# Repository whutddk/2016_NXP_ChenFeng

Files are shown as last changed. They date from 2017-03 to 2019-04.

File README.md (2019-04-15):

# 2016年恩智浦杯全国大学生智能汽车大赛 

-------------------------------

* 有了前一年参赛的经验，更有了资金和赛道，一切就变得特别顺利
* 加入汽车学院参加比赛
* 参与其中的电轨竞速组和电轨节能组，拿下两个全国一等奖
    - 电轨竞速组负责：电路；代码工程搭建、验证、规范化；控制算法搭建、验证；传感器解决方案
    - 电轨节能组负责：电路；取电方案

----------------------------

### 背景
* 2016是比赛的改革年，出现了很多新组别（电轨，信标，双车超车）
* 我们参与的电轨组组别太新，规则摇摆不定
    - 是否取电
    - 传感器方案
* 赛初即做了取电解决方案，后来该方案移动至创意组。鉴于我校从来没有队伍参与创意（不知道保研政策），我们决定第一年试水创意，将创意作为备份组。

### 过程
* 这个组难点在传感器方案，官方给出的传统三点震荡方案很早进行了验证，距离太短。参考TI，LDC系列传感器，把所有手册看了一遍，发现LDC1614和LDC1314的方案最合适，评估版价格相同，选择精度更高的LDC1614。
* 区别于电磁，金属传感器只能看见线圈下面的赛道情况，没有电磁波传播的扩展，所以视角相对较小。前瞻越长，视角越小，控制越容易发散。
* 双线圈方案与三线圈方案
    - 传感器非线性问题非常严重，这一年探讨了非常多拟合线性化方案
    - 因为双线圈拟合有对称问题，改用三线圈拟合
* 控制
    - 舵机方向控制
        + 简单三参数PD
        + 因为队友机械能力很强，机械上大量非线性问题都解决了，简单的PID方向控制即可取得非常好的效果
    - 电机调速
        + 增量式PI
* 算法
    - 探讨过模糊控制并进行验证，因为风险较大，后面放弃使用
    - 后面采用简单PID加BNAG-BANG法进行控制
* 总结：如果要我总结智能车赛的三个要点
    - 全程参数线性化
        + 无论是修理机械，调整传感器，PID分段等，传感器多项式拟合，讨论的是线性控制，将非线性环节用各种手段处理掉，调参就很简单了
    - 保证控制实时性
        + 使用Cortex-M4处理器，运算主要集中在解算拟合函数，未使用到DSP，只要不使用模糊控制，我们组的控制实时裕量还是很足的（当然我自己也是验证过的）
        + 整个组的控制周期瓶颈在舵机上，只能50HZ控制，超过了及其不稳定
        + 电流环，我反对让学弟花太多精力去搞，主要是实时性难以保证，而学弟意识不到这个问题，在这里解释一下
    - 构造合适实验验证问题
        + 静电干扰复位原因
        + 起跑线干簧管误触发原因
        + LDC1614复位原因
        + 电机Bang-Bang控制对传感器，电路板的冲击
    
### 照片
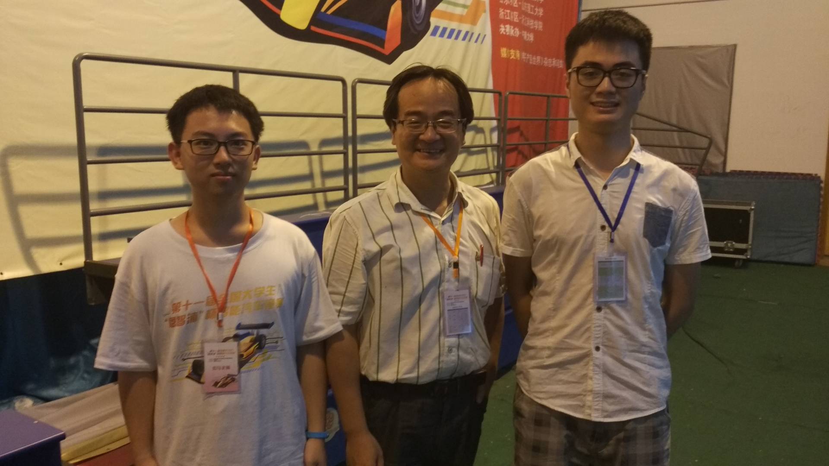
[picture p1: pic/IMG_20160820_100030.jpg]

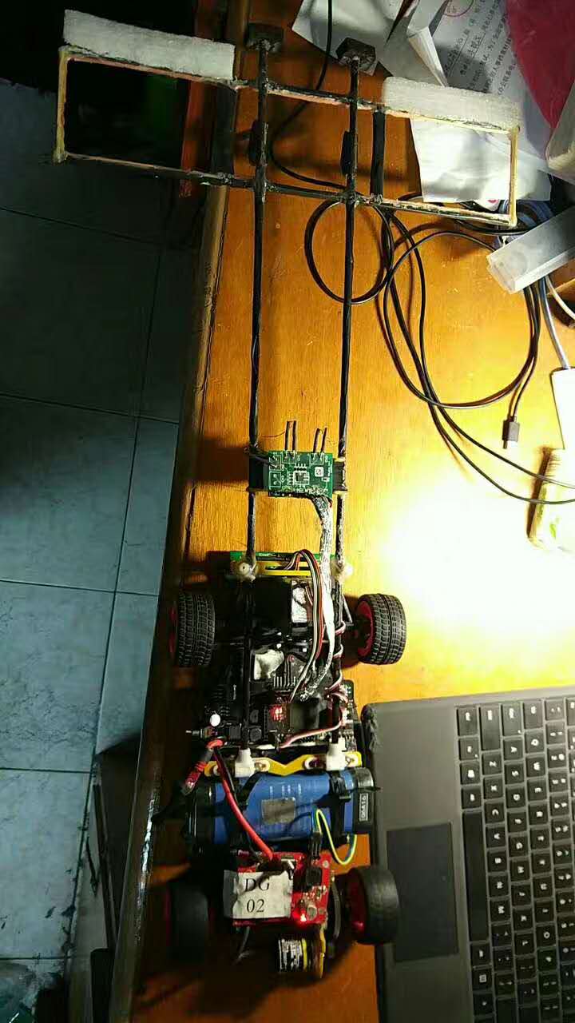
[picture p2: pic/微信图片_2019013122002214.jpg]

合照

### Video
* [省赛（华南赛）预赛](https://v.youku.com/v_show/id_XMTY0ODY4NTUyOA==.html?spm=a2hfx.9903432.collectVideo.5~5~5~1!2~3~A
)
* [省赛（华南赛）决赛](https://v.youku.com/v_show/id_XMTY0OTQxNjM4NA==.html?spm=a2hfx.9903432.collectVideo.5~5!2~5~1!2~3~A)
* [国赛决赛第二次成功](http://v.youku.com/v_show/id_XMzc4NzQyMTY5Ng==.html?spm=a2h3j.8428770.3416059.1)
* [国赛决赛第二视角](https://v.youku.com/v_show/id_XMTY5MTkyMTg3Ng==.html?spm=a2hfx.9903432.collectVideo.5~5!3~5~1!2~3~A)

## Contributors

* 电轨竞速组
  - Yansong Zhang
  - Jiawei Yuan
  - Ruige Lee
  
* 电轨节能组
  - Ruige Lee
  - Yansong Zhang
  - Cong Chen
  - Song Feng （学弟）
  - Rong Huang （学弟）
  - Jiawei Yuan

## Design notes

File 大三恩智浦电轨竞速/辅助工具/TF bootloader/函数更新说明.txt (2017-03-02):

删掉 exti ，改成用 port 来配置端口属性，可配置 DMA触发、中断、端口上拉下拉电阻、滤波等功能。修改了DMA的接口，DMA_PORTx2BUFF_Init 和 DMA_count_Init 后面，都需要调用 port_init 来配置端口属性。

例如配置中断：
port_init(PTA29,IRQ_RISING | PULLUP | PF);    //PTA29中断，下拉，下降沿触发中断，带滤波

例如配置DMA：
DMA_PORTx2BUFF_Init(CAMERA_DMA_CH, (void *)&PTB_BYTE0_IN, (void *)IMG_BUFF, PTB8, DMA_BYTE1, CAMERA_SIZE , KEEPON);
port_init(PTB8,DMA_RISING | PULLUP );

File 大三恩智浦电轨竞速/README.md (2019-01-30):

* 本资料由武汉理工大学 电工电子中心，李锐戈整理
* 除基于学长的上位机加密不对外，其余遵循本repo的LICENCE

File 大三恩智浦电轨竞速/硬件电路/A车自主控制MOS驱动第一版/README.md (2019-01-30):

* 本届不限制主控数量，因此，设想一种新方案，独立出一块主控用于单独的电机控制，使用更多的资源，做更复杂的电机算法。此方案因为主控板设计不合格被终止。
* 做电流环的时机不成熟

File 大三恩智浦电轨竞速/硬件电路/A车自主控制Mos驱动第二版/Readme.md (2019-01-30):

* 本届不限制主控数量，因此，设想一种新方案，独立出一块主控用于单独的电机控制，使用更多的资源，做更复杂的电机算法。此方案因为主控板设计不合格被终止。
* 当时电流环控制的理论不够充足。并没有做电流环控制的条件

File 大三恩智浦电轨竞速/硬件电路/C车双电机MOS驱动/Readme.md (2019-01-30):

* C车ccd的mos驱动，跟蓝宙的没什么区别，画出来就换组了，根本没有焊接和测试过该电路

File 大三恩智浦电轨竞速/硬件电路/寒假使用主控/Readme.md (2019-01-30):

* 寒假期间使用的主控，四层板，集成了LDC1614，但无法使用
* LDC1614 不能使用主要是因为封装不好处理，当时没有处理QFN的条件，也失败不起，芯片太贵了

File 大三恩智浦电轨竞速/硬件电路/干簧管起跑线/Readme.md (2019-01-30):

* 非光学组的起跑线，终点线识别都是靠磁铁标记，使用干簧管识别
* 一直有误触发的问题，没到终点就停了
* 信号也上拉了，怀疑是震动，改了很多版本，最后使用的是多路仲裁加延时屏蔽的方法保护

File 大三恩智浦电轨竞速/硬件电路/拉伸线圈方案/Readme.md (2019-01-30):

* 对于电轨组的识别铝膜的导航方式，我把TI的LDC系列的所有手册都看了，主要手册也翻译了
* 有一种解决方案为PCB线圈，再分对称线圈和拉伸线圈

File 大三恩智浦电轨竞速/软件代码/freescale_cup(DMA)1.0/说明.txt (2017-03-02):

使用DMA采集三点震荡脉冲数
原理：DMA开启后，每触发一次，一个寄存器将会自减，因此，开启DMA后，使用io触发DMA，随意进行一次传输，时间到后，读取寄存器并与初始值对比。

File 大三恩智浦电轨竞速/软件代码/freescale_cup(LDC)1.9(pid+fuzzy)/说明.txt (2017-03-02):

代入了在线模糊控制代码，可以配合上位机进行模糊控制，开启模糊控制还是pid差一个宏定义

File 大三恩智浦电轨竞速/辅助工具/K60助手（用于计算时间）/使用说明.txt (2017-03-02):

LPLD_K60_Tool是一个可以计算ADC采样速率、IIC频率、SPI频率的小软件。

软件中的所有"选项"均是OSKinetis固件库中初始化"结构体的变量"
你只要选择相应的值，就可以实际运行的结果
同样，只要的结构体变量输入这些选项值，实际运行结果就是计算结果

拉普兰德
http://www.lpld.cn

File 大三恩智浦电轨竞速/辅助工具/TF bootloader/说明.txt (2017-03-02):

这个工程是野火的K60 TF卡bootloader程序，能够从SD卡中下载程序到处理器
这一年没时间研究，理论上移植完成后，在比赛时，只要掉包了SD卡，既可以替换掉程序。

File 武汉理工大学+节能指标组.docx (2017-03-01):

第十一届“恩智浦”杯全国大学生智能汽车竞赛节能指标组

技术报告

学 校： 武汉理工大学

队伍名称： 晨风队

参赛队员： 李锐戈

张艳松

成聪

冯松

黄荣

带队教师： 邹斌

# 目录

# 第一章引言

# 1.1 背景介绍

小小的神奇车模驰骋在暑期各个竞速赛场已过十年，花样翻新智能汽车创意比赛之花也绽放了八年。第十一届全国大学生智能汽车竞赛将继续举办创意组比赛，比赛分为两个组：节能指标组和物联网主题组。其中，节能指标组要求是训练同学能够设计低功耗、节能的运动平台。需要综合机械结构、电路设计、控制方法设计一台节能的智能车。竞赛过程会对电源输送至电轨直流电能进行计量。计量方法是每一毫秒进行累计电源输送至电轨的电流和电压的乘积。直流电源无法回收电能。

比赛排名根据赛车在规定三分钟时间内完成一周所消耗的电能和运行时间分别进行排名。将两项排名名次相加之后，再进行综合成绩排名。

# 第二章机械系统设计及实现

# 2.1整体布局

经过对竞速电轨组的学习和研究，我们决定用环氧树脂板雕刻一个适当镂空的智能车底盘，用于相关硬件电路模块的装配（相关模块有电机驱动模块、主控板、传感器采集模块、电容储电模块、万向轮、传感器支架以及电机支架等）。与A车模电轨组类似，取电部分由两片v型弹簧片连接加长，整车质量靠后，集中在后车轮轴上，以增大后轮的摩檫力，进而增大整车的驱动力，前端有一定伸长量的传感器线圈获取赛道信息，中间是主控板，后端即是电机驱动部分，与两驱动轮相邻。如图2.1.1:

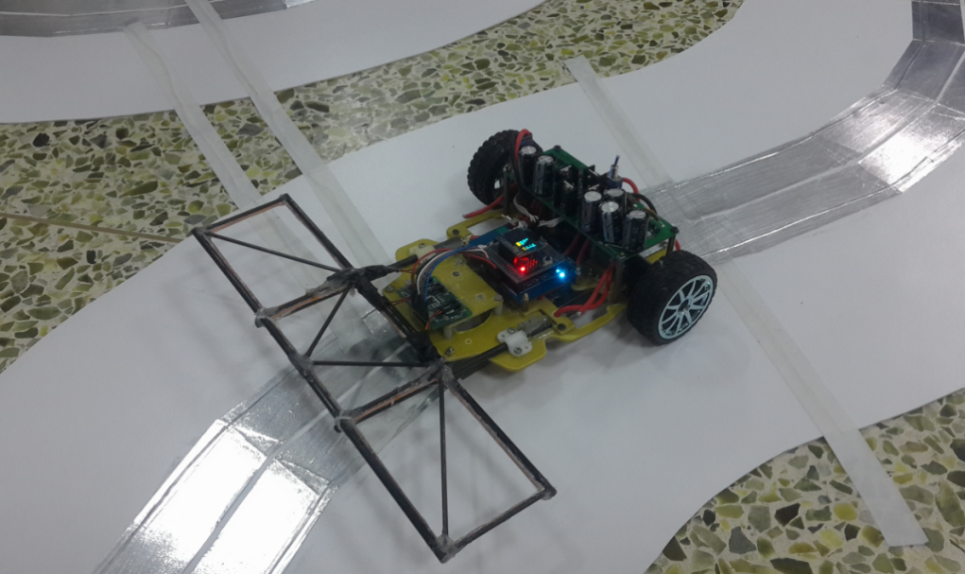
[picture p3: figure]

图2.1.1整车实物图

在实现做出相关模块后，为了达到高精度的装配效果，防止发生干涉现象，我们在catia v5R20软件里进行了建模仿真，各模块均用量具测量再输入，最终整体布局如下（传感器线圈模块未显示，应该在固联在两根伸长的碳素杆上面）,如图2.1.2、2.1.3：

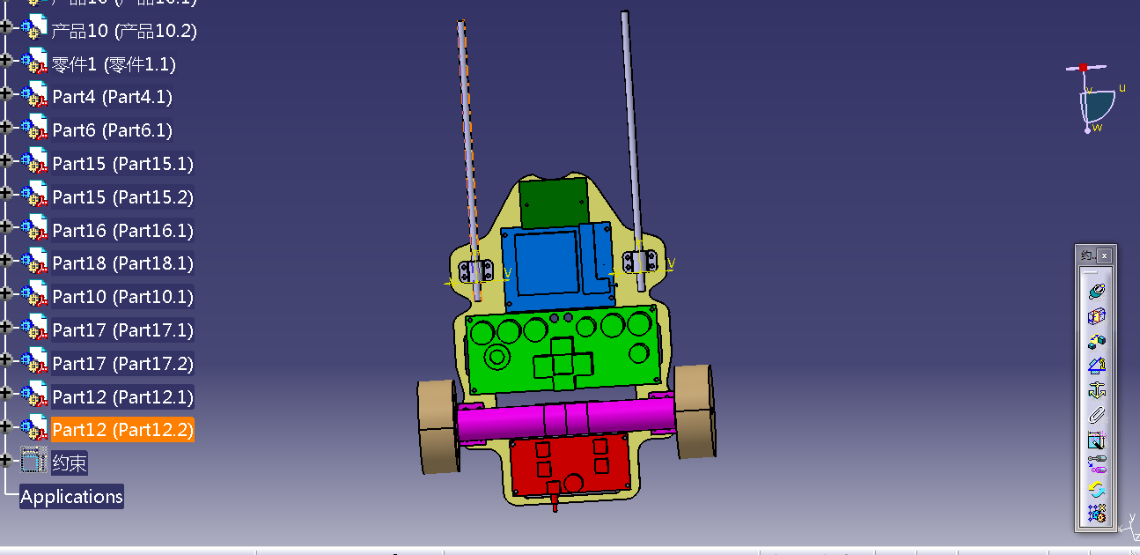
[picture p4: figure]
截图1

图2.1.2俯视图

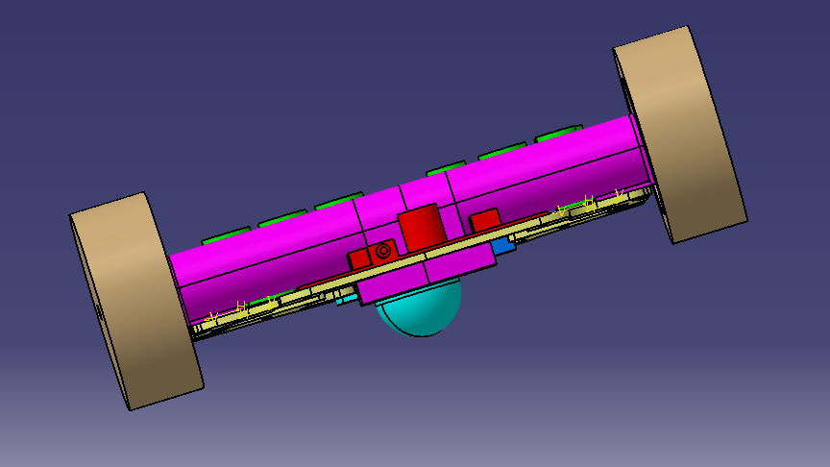
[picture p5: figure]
截图3

图2.1.3后视图

# 2.2智能车底盘设计

方案一：

为了方便模块的安装（原有安装孔）、减少车重及降低重心的原则，底盘精良精简，能不必要的地方均镂空处理，同时又要有一定外观，所以设计时几乎都是圆滑过渡，这同时也减少了底盘的应力集中二炸裂，增强实用性，底盘初稿（cad绘图设计）如图2.2.1：

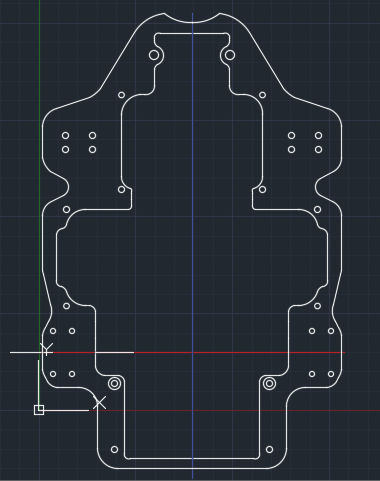
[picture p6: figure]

图2.2.1底盘CAD示意图

经过装配后，发现效果并不是很好，由于测量误差的影响，电机安装到底盘后，两轴并不重合，成一个小夹角，，并且底盘虽然横向刚度满足要求，但纵向（行车方向）刚度太小，挠度过大，于是有设计一块底盘加固板与电机正下方，一方面加强纵向刚度，一方面加以附属电机的长轴，使之与底盘平面平行，左右两轴轴线重合，改善行驶效率（加强件上除了固定用的安装孔外还有两组小圆孔，用于穿过扎带约束电机长轴而固定在底盘上）如图2.2.2：

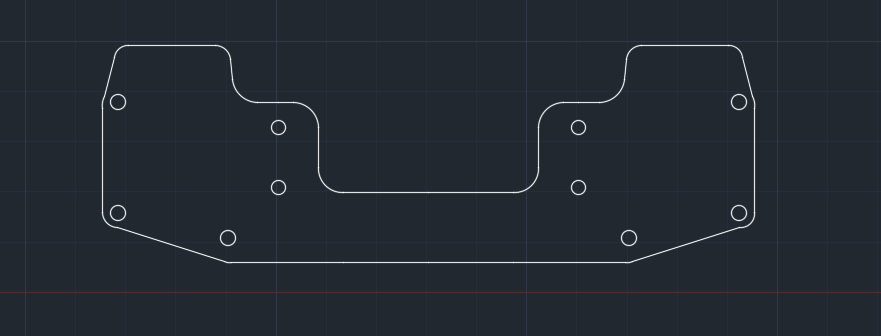
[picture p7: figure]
底盘

图2.2.2底盘加强件CAD示意图

方案二：

取电用的弹簧片最初做成“U”型安装在底盘电机下方，做好后在跑的过程中发现几个问题，一是弹簧片的反作用力太大，减小车轮的支撑力，以至于车轮的摩擦力很小，会出现左右车轮受力不均匀的情况，甚至无法驱动小车前进；二是在上下坡的时候，速度如果不够快，整个小车就会被“挂”在坡道上，这也是由于弹簧片的刚度太大原因。由此我们改进了弹簧片的使用方法，即将两片弹簧片连接加长。小车底盘的形状如图2.2.3：

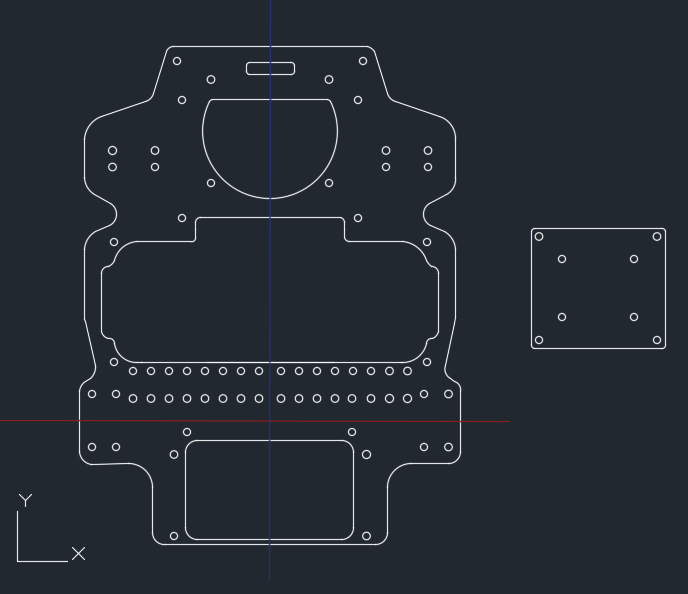
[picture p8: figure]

图2.2.3新版底盘CAD示意图

两片V型弹簧片连接加长作为取电装置，加长的弹簧片弹性更好，更加适合用于小车取电。实物图2.2.4：

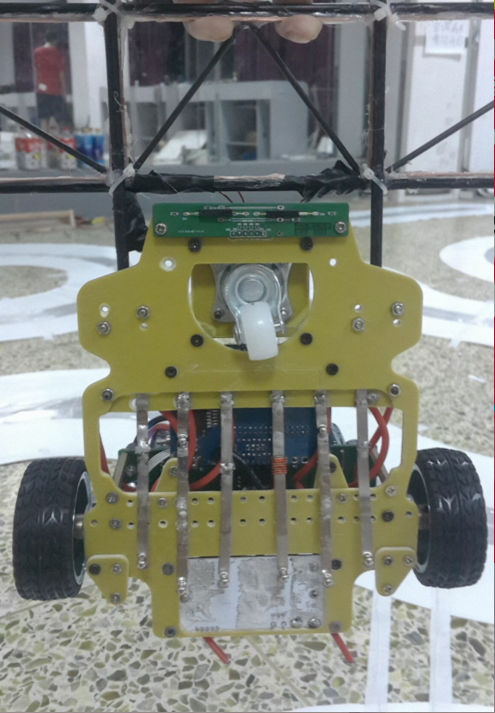
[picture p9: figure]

图2.2.4底盘实物图

# 2.3电机装配

由于所选电机与编码器（减速机构和测速机构）固联为一体，为降低重心，突出的部分尽量朝下，然后电机装在L型金属支架上，防止移动，用螺母将支架固定在底盘上，完成电机的安装，如图2.3.1-2.3.3：

图2.3.1 L型电机支架

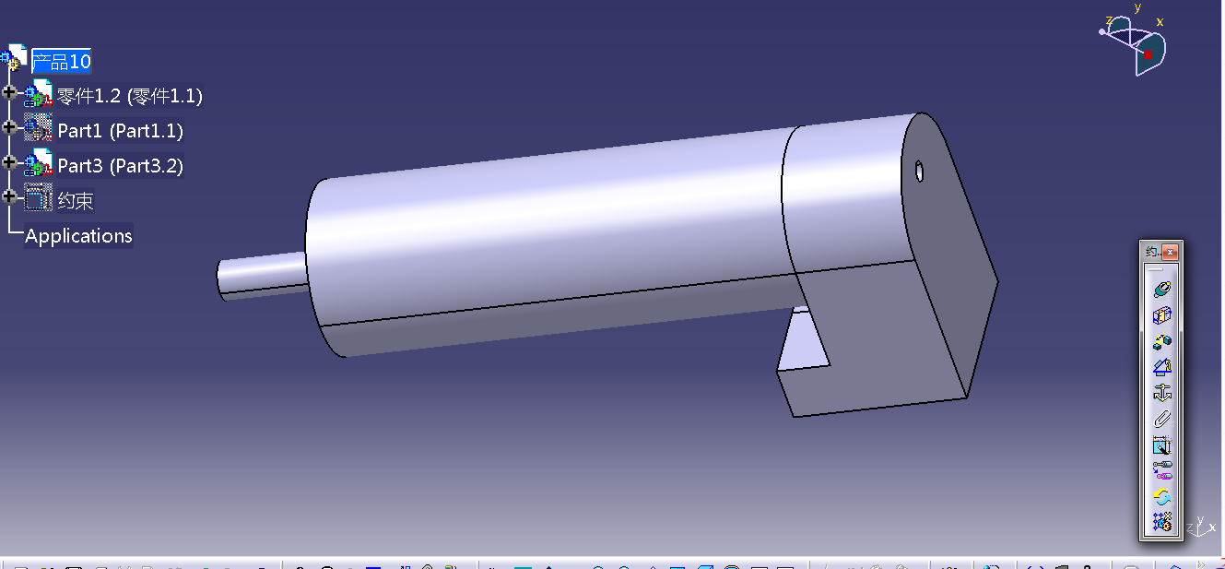
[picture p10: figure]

图2.3.2 电机

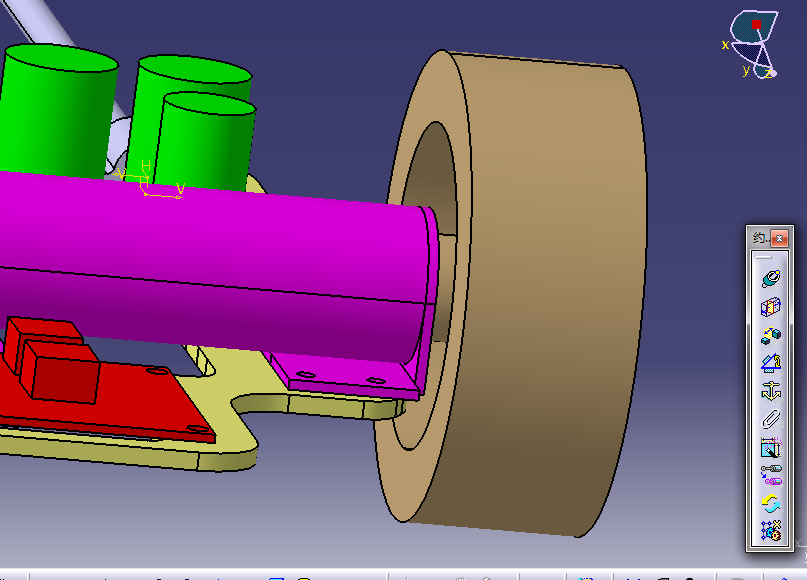
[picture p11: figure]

图2.3.3 电机装配示意图

# 2.4前瞻固定

直接用碳素杆和安装孔固定在底盘两边的空余地方上如图2.4.1-2.4.3：

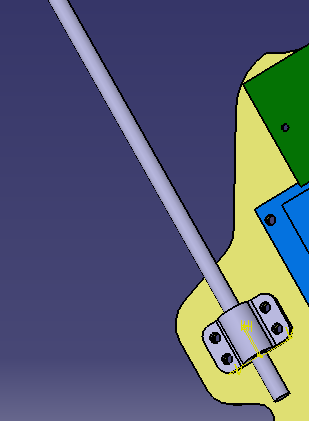
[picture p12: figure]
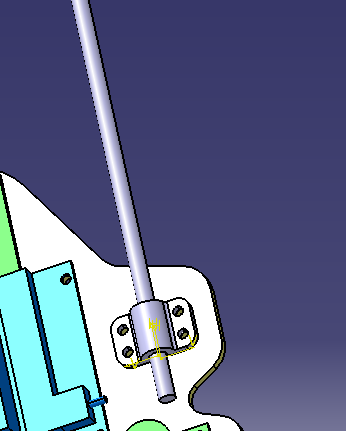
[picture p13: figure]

图2.4.1 碳素杆固定示意图一 图2.4.2碳素钢固定示意图二

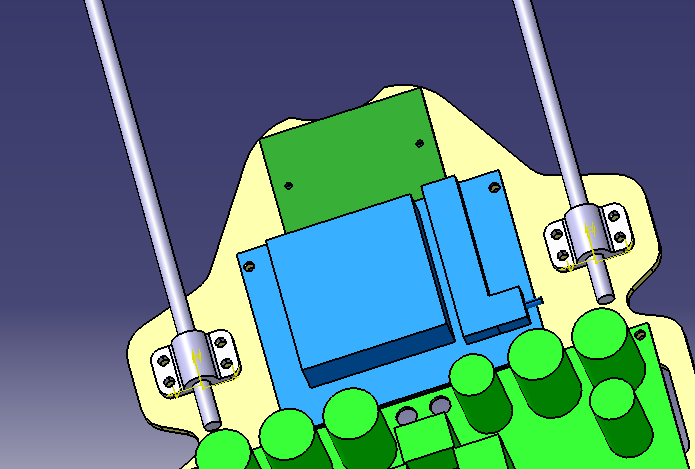
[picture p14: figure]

图2.4.3 碳素杆固定示意图三

# 2.5万向轮安装

固定在底盘下底面直接与赛道接触。采用如下图（行车方向前端）所示的万向轮：

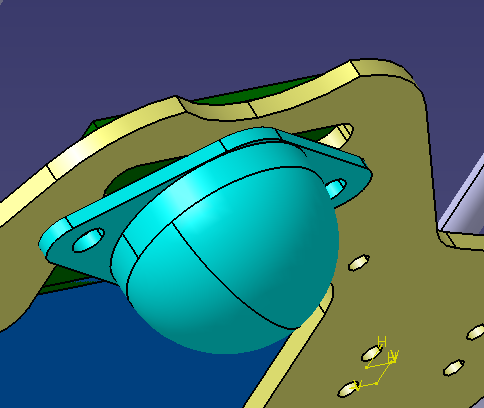
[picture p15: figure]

图2.5.1 万向轮安装示意图一

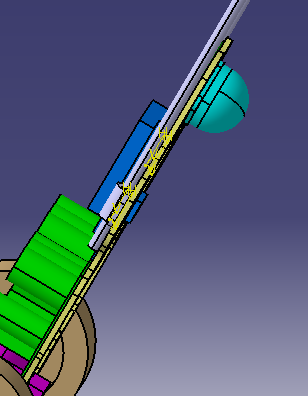
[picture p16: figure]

图2.5.2 万向轮安装示意图二

在前期使用的过程中发现这种万向轮的阻力较大，万向轮里的钢珠滚动不顺畅，因此我们改为类似下图所示的万向轮。

图2.5.3万向轮示意图

机械部分如上所述。

第三章硬件电路设计

# 3.1整流电路

由于赛道上两个导电铝膜所给的电压正负极无法确定，因此系统取电模块需要进行电源极性矫正，即电刷取电之后需要经过一个二极管全桥整流。考虑到用肖特基二极管有0.3V的压降（SK34），因此搭建的整流桥会产生约0.6V的电压损耗。假设系统正常工作电流2A，则在整流部分将会有0.6W的功率以热能的形式耗散。

采用理想二极管整流桥控制器LT4320。配合4个N沟道MOSFET,搭建整流桥，作为主整流电路。

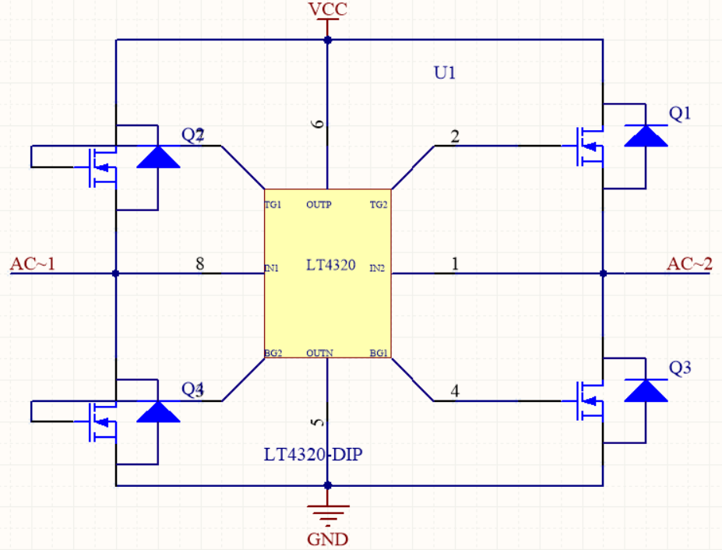
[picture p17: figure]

图3.1.1理想二极管整流电路图

每个MOSFET开通后内阻3.3mOhm，所以整流桥内阻约6.6mOhm。在同样2A的工作电流下，耗散功率如公式1：

（公式1）

为肖特基二极管搭建整流桥的约1.5%。其中P为耗散功率，I为电流大小，R为整流桥内阻。

当输入电压小于LT4320的工作电压（9V）时，LT4320不工作，所有MOSFET不开通，电路通过MOSFET内部的二极管进行整流。整流桥压降约1V。

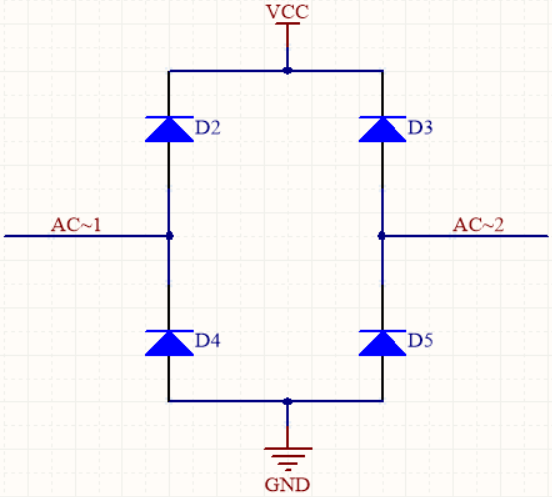
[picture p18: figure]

图3.1.2寄生二极管整流电路图

两段铝膜之间间距仅为5mm，为防止车身偏移导致一个电刷短路两段铝膜，每个电刷接触点不能大于5mm。考虑到只有一对小电刷参与取电对稳定性有很大影响，决定在LT4320理想二极管整流桥作为主整流器的前提下，增加8个使用肖特基二极管整流的电刷作为辅助整流电路。

每个电刷正反连接一个肖特基二极管，当任意两个电刷接触了正负极铝膜，且LT4320理想二极管整流器没有工作，四个肖特基二极管组成一个整流桥，进行辅助整流，确保供电稳定。

图3.1.3辅助电刷

# 3.2大电容储能

考虑到在十字交叉部分或者其他意外断路可能造成暂时的断电，为此，在整流之后加入大电容进行储能。以保证在断电后能够维持系统工作一段时间。同时，在加入大电容后，容性负载上电瞬间将会产生很大的电流，有引起赛道电源断电的可能。因此我们在电路中串入一个功率电感，和一个自恢复保险管来抑制电流的过快上升。电容所储存的能量将被计算在功耗中，因此电容量不应该过大，以减小总功耗。

# 3.3 Buck变换和线性稳压电路

赛道电源提供12V直流电。但主控电路需要的电压主要为5V和3.3V。从12V降压到5V，如果使用线性稳压,假设主控电路消耗电流500mA，如公式2：

（公式2）

将会有约3.5W功率以热能形式耗散。其中P为耗散功率，为输入电压，为输出电压。采用buck电路将12V开关稳压到5V更加节能。

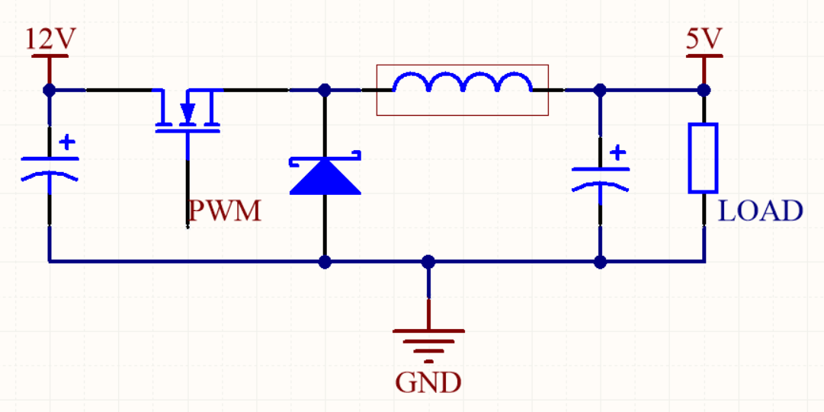
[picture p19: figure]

图3.3.1buck变换电路示意图

假设buck变换的效率为80%（参考LM2596-5（TI）），参考公式3：

（公式3）

则buck变换的开关损耗为0.625w，为线性稳压的17.8%。其中为效率。

使用开关稳压方案将给电源带来比较大的纹波，对主控及传感器的工作将有一定的影响。因此，使用线性稳压芯片，将5V经电容滤波后稳压到3.3V供给处理器和传感器使用。

图3.3.2线性稳压电路图

# 3.4取电方案

取电需要较多小电刷，而且需要电刷对赛道有一定压力以保证接触良好。为此采用弹簧片以保证取电的稳定性。同时，金属弹簧片电阻很小，对电机机械特性几乎无影响。

图3.5.1弹簧片图

# 3.6主控方案

采用恩智浦Kinetis L系列超低功率微处理器，并在使用时根据需求适当采用降低内核频率，进入低功耗模式，关闭多余的外设时钟，合理进行任务调度，进入等待模式等方法降低系统功耗。

# 第四章控制软件设计说明

# 4.1程序流程图

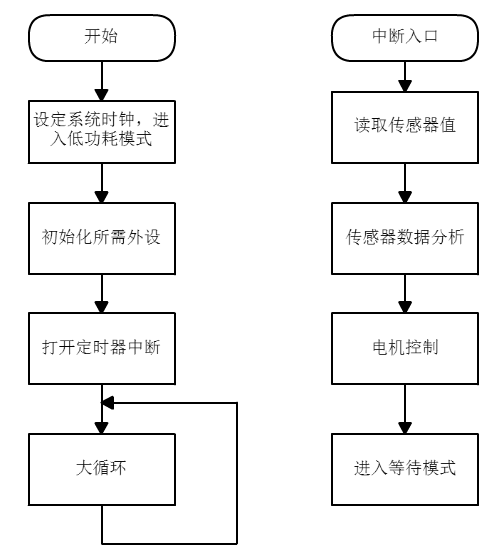
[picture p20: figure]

图4.1.1程序流程图

# 4.2低功耗模式设置

KL25系列处理器具有RUN、WAIT、STOP、VLPR、VLPW、VLPS、LLS、VLLS3、VLLS1、VLLS0，10种电源模式。按ARM模式大类分有Run，Sleep，Deep Sleep三种模式。为了减小处理器功耗，需要在算法运算处理的时候工作在Run模式下，处理完成后进入Sleep模式降低功耗。为了获得更低的功耗，可以优化控制算法，使对总线时钟频率的需求降低，从而可以进入更低功耗的VLPR模式，当处理完毕后，进入更低功耗的VLPW模式。

要进入低功耗模式，首先要对系统的时钟状态进行设置。如图4.2.1：

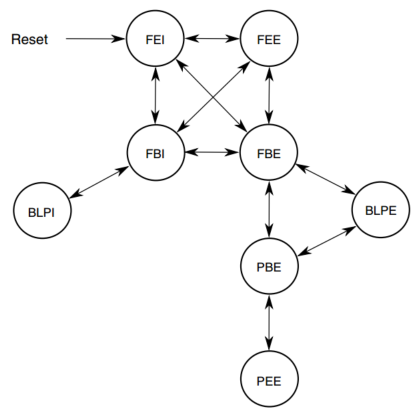
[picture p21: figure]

图4.2.1 KL25多用途时钟发生器状态图

由状态图可知，系统复位后，首先进入FEI模式，要进入VLPR电源模式，必须让时钟状态处在BLPI或者BLPE模式。因此首先需要把时钟从FEI转到FBI，再从FBI转到BLPI模式，并使用内部4MHz快速时钟源。设置分频系数后，让内核时钟频率达到4MHz，总线时钟频率1MHz。

在控制时，将串口，ADC等多余的外设失能，在控制算法允许的条件下将传感器数据采集和电机控制的周期加长，增加VLPW状态的占比以获得更低的功耗。

使用“恩智浦”提供的微控制器功耗预计工具，可以分别计算处理前后功耗的差距。

图4.2.2正常模式功耗计算图

图4.2.3低功耗模式功耗计算图

# 4.3循迹算法

赛道是由两条铝膜构成，通过线圈检测铝膜的位置来判断小车所在的位置。通过读取LDC1614寄存器的值，得到三个线圈与各自电容组成的谐振电路的振荡频率。当线圈下方有金属铝膜时，谐振频率会发生改变，且变化大小和覆盖面积有关。

因此我们通过静态采集小车与赛道偏移位置的大小与三个线圈两两读数之差的关系，获得一系列数据点，并进行三次多项式拟合。得到线圈读数和小车位置的多个关系公式，再用一些特征点最终判断小车的正确位置。

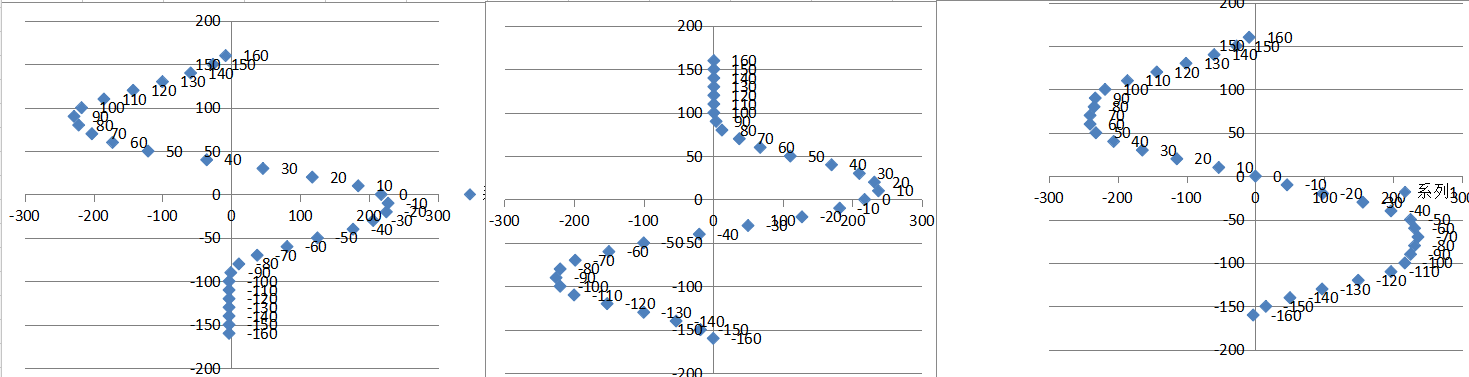
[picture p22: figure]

图4.3.1赛道检测拟合示意图

# 4.4速度和转向控制

小车是由两个伺服电机和一个支撑用万向轮组成的。在允许的调速范围内，可以使用增量式PI算法，分别控制两个电机的转速。在实际赛道上，首先设定一个基础速度，在弯道时，使用外环的pid根据当前位置偏差获得一个差速值，将此差速值分别正负叠加到速度内环的给定上，使左右轮产生差速从而实现转弯。

# 第五章开发工具调试过程说明

# 5.1电能检测装置

为了测量运行过程中消耗的电能，我们独立设计了一个嵌入式电能检测控制系统。

该系统采用K60处理器，独立电源供电，经过霍尔电流检测芯片ACS712-5实时监测赛道上的电流。通过电磁继电器控制赛道的通电与否。

系统上电时，在断开电源状态下连续采集电流传感器零点，完成后闭合继电器，给赛道上电，对电流进行积分，并使用OLED显示电能消耗情况.赛车出发后，检测是否过流，如发生过流，关闭继电器并报警。延时2秒后重新闭合继电器。

# 第六章模型车的主要技术参数说明

# 6.1智能车外形参数

长35cm，宽22cm，高3cm。

# 6.2电路部分参数

6个电解电容储能约0.03F,正常工作功率6W。

# 6.3传感器个数以及种类

3个漆包线线圈，2个编码器，3个干簧管。

# 6.4赛道信息检测精度，频率

检测精度1cm，频率20ms。

# 6.5电机参数和选型

电机励磁方式为他励，转矩和电流成正比，同时电枢回路电阻尽量小，能够获得更加硬的机械特性。

将待测电机和同一个电机同轴连接。待测电机直接接到12V稳压源，工作在正向电动状态，另一个电机的电枢串联功率电位器，工作在发电状态。调节电位器，调整发电机负载从空载到重载，记录电动机电枢电流大小和转速。测试几种电机特性

## 6.5.1带减速箱的maxon空心杯电机

电机电枢内阻为5.8Ω，额定电压为12V，因此在12V下带减速箱测试其特性曲线，数据如下：

表6.5.1Maxon空心杯电机测试数据

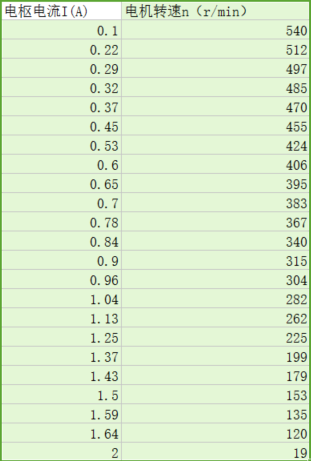
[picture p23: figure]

使用Matlab对特性曲线进行拟合，结果如图6.5.1.1：

图6.5.1.1Maxon空心杯电机特性曲线

由测试数据可以得到公式4：

（公式4）

其中n为电动机转速，I为电枢回路电流大小。

由此可知该电机在带减速箱外接12V电压的情况下的理想空载转速为574r/min，电磁转矩常数，如公式5：

（公式5）

其中为电磁转矩常数，为励磁大小。

## 6.5.2 RS-380电机性能测试

由于该电机电流较大，实验室设备功率有限，所以采用降电压测试，再用公式推算的方法。在1.19V下测试数据如下：

表6.5.2.1RS-380电机测试数据

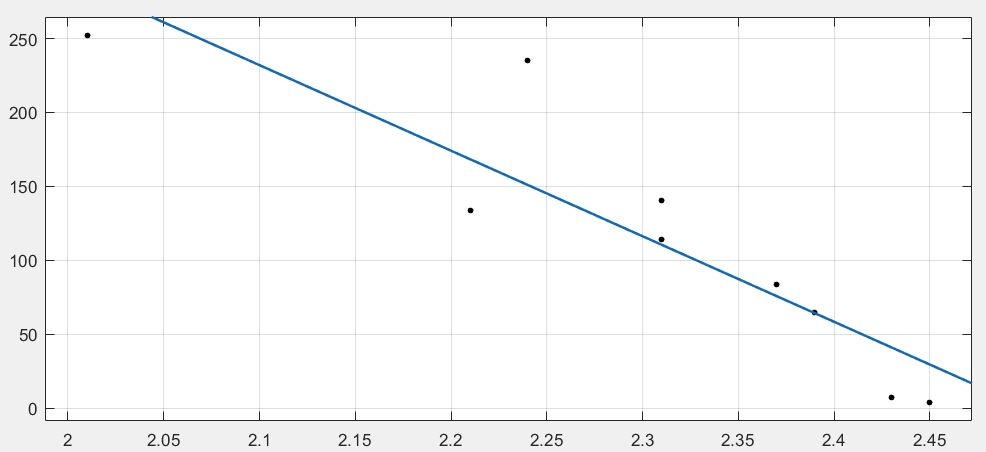
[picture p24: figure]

图6.5.2.1RS-380电机特性曲线

由测试数据可以得到公式6：

（公式6）

计算可得公式7：

（公式7）

由此可以推算该电机在12V时的特性如公式8：

（公式8）

参考规则要求，选用maxon电机更为合适。

# 第七章结论与反思

作品设计为采用LT4320和四个场效应管搭建的理想二极管整流桥的主整流装置和多组肖特基二极管的辅助整流装置对赛道电源做极性矫正，最大限度消除了二极管压降带来的损耗，同时尽可能保证取电的稳定性。采用buck变换将电压从12V稳压到5V，使用线性稳压将5V稳压到3.3V,最大限度地减小能耗并抑制电源纹波。处理器采用恩智浦公司的KL25系列低功耗微处理器，合理运用了低功耗模式，设置系统时钟，最大限度地降低了系统功耗。作品采用两个空心杯伺服电机差速驱动，并用一个球式万向轮支撑，在速度和功耗上取得平衡。循迹采用LDC系列电感数字传感器，能够非常精确地识别赛道。

在这几个月的准备过程中，我们感到通过创意赛大大提高了自己的工程实践能力和创造能力。学会了根据实际需要，设计合适的电路。并对电力电子有了初步的认识。

在这几个月的备战中，在场地、经费方面都的到了学校的大力支持，在此特别感谢一直支持和关注智能车比赛的学校领导以及各位老师。同时也感谢比赛组委会能组织这样一项很有意义的比赛。

# 参考文献

[1]阮毅陈伯时电力拖动自动控制系统——运动控制系统机械工业出版社 2015

[2]李发海王岩电机与拖动基础清华大学出版社 2013

[3]胡寿松自动控制原理科学出版社 2013

[4]王兆安、刘进军主编.电力电子技术.北京:机械工业出版社,2009.5

[5]谭浩强C 语言程序设计[M]，北京：清华大学出版社. 2005 年7 月第三版

[6]童诗白，华成英．模拟电子技术基础[M]．北京. 高等教育出版社．2000

[7]陶永华 新型 PID 控制及其应用，机械工业出版社，2002

[8]仇慎谦，PID 调节规律和过程控制，江苏科学技术出版社，1987.12

# 附录A

## 电机驱动

图A-1电机驱动电路图

## 取电电路

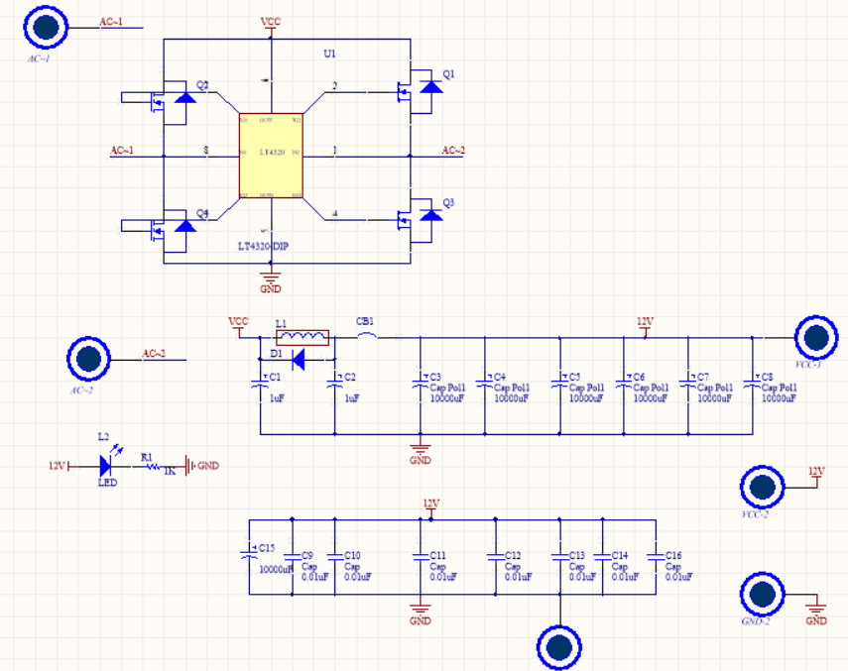
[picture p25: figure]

图A-2取电电路图

## 主控电路

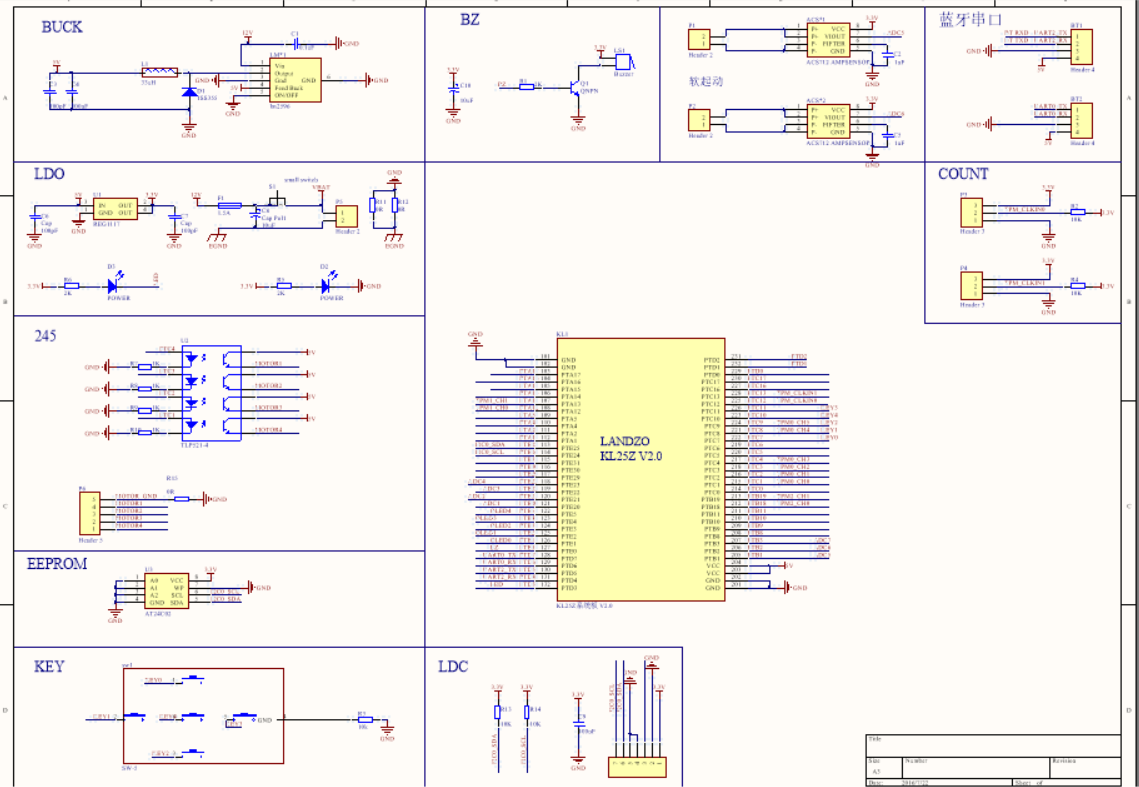
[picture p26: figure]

图A-3主控电路图

# 附录B

进入BLPI模式代码：

MCG_C1 = MCG_C1 | MCG_C1_CLKS(1) ;

while( !( MCG_S & MCG_S_CLKST(1)) );

/* Wait and check status. */

while (!( MCG_S & MCG_S_IREFST_MASK));

MCG_C2 = MCG_C2 & ~MCG_C2_LP_MASK;

MCG_C6 = MCG_C6 & ~MCG_C6_PLLS_MASK;

MCG_C2 = MCG_C2 | MCG_C2_LP_MASK;

MCG_C2 |= MCG_C2_IRCS_MASK;

MCG_C1 |= MCG_C1_IRCLKEN_MASK;

#define SIM_SOPT2_PLLFLLSEL(x) (((uint32_t)(((uint32_t)(x)) << SIM_SOPT2_PLLFLLSEL_SHIFT)) & SIM_SOPT2_PLLFLLSEL_MASK)

MCG_SC = 0;

SIM_CLKDIV1 = 0x00030000U;

SIM_SOPT2 = ((SIM_SOPT2 & ~SIM_SOPT2_PLLFLLSEL_MASK) | SIM_SOPT2_PLLFLLSEL(0U));

SIM_SOPT1 = ((SIM_SOPT1 & ~SIM_SOPT1_OSC32KSEL_MASK) | SIM_SOPT1_OSC32KSEL(3U));

core_clk_mhz = 4;

core_clk_khz = core_clk_mhz * 1000;

bus_clk_khz = core_clk_khz / (((SIM_CLKDIV1 & SIM_CLKDIV1_OUTDIV4_MASK) >> 16) +1);

进入VLPR模式代码：

SMC_PMPROT = SMC_PMPROT | SMC_PMPROT_AVLP_MASK;

SMC_PMCTRL = SMC_PMCTRL | SMC_PMCTRL_RUNM(2);

while(SMC_PMSTAT != 0x04);//进入VLPR

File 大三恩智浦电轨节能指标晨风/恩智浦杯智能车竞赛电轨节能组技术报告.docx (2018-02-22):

第十一届“恩智浦”杯全国大学生智能汽车竞赛节能指标组

技术报告


学 校： 武汉理工大学

队伍名称： 晨风队

参赛队员： 李锐戈

张艳松

成聪

冯松

黄荣

带队教师： 邹斌

关于技术报告和研究论文使用授权的说明

本人完全了解第十一届“恩智浦”杯全国大学生智能汽车竞赛关于保留、使用技术报告和研究论文的规定，即：参赛作品著作权归参赛者本人，比赛组委会和“恩智浦”半导体公司可以在相关主页上收录并公开参赛作品的设计方案、技术报告以及参赛模型车的视频、图像资料，并将相关内容编纂收录在组委会出版论文集中。

参赛队员签名：________________

带队老师签名：________________

日 期：________________

目录

第一章 引言…………………………………………………….….1

1.1 背景介绍……………………………………..…………….1

# 第二章 机械系统设计及实现………………………………………1

2.1整体布局……………………………………………………1

2.2智能车底盘设计………………………………………….…3

2.3电机装配…………………………………………………….4

2.4前瞻固定………………………………………………..…..5

2.5万向轮安装…………………………………………...….…6

# 第三章 硬件电路设计………………………….……………….….8

3.1整流部分……………….……………….………….……..…8

3.2大电容储能…………….……………….………….……..…9

3.3 Buck变换……………………………………………...……9

3.4电动机软起动，电流环准时间最优控制反馈电路…………10

3.5取电方案…………………………………………………...10

3.5.1使用碳刷取电…………………………………………....10

3.5.2使用单根导线…………………………………………....11

3.5.3采用集束导线…………………………………………....11

3.6主控方案…………………………………………………...12

# 第四章 控制软件设计说明……………………………...……...…12

4.1程序流程图………………………………………………...12

4.2循迹算法…………………………………………………...12

4.3速度和转向控制………………………………….………...13

# 第五章 开发工具调试过程说明……………...…………...………13

5.1电能检测装置……………………………………………..13

# 第六章 模型车的主要技术参数说明……………...………………13

6.1智能车外形参数…………………………………………...13

6.2电路部分参数……………………………………………...13

6.3传感器个数以及种类……………………………………...13

6.4赛道信息检测精度，频率………………..………………..13

6.5电机参数和选型…………………………….….………….14

6.5.1带减速箱的maxon空心杯电机……………….………….14

6.5.2 RS-380电机性能测试…………………...….………….15

第七章 结论与反思……………………………….………....…….16

附录…………………………………………………….…….…….16

电机驱动图……………………………………………...……….16

取电电路图……………………………………………...……….17

主控电路图……………………………………………...……….17

# 第一章 引言

1.1 背景介绍

小小的神奇车模驰骋在暑期各个竞速赛场已过十年，花样翻新智能汽车创意比赛之花也绽放了八年。第十一届全国大学生智能汽车竞赛将继续举办创意组比赛，比赛分为两个组：节能指标组和物联网主题组。其中，节能指标组要求是训练同学能够设计低功耗、节能的运动平台。需要综合机械结构、电路设计、控制方法设计一台节能的智能车。竞赛过程会对电源输送至电轨直流电能进行计量。计量方法是每一毫秒进行累计电源输送至电轨的电流和电压的乘积。直流电源无法回收电能。

比赛排名根据赛车在规定三分钟时间内完成一周所消耗的电能和运行时间分别进行排名。将两项排名名次相加之后，再进行综合成绩排名。

# 第二章 机械系统设计及实现

## 2.1整体布局

经过对竞速电轨组的学习和研究，我们决定用环氧树脂板雕刻一个适当镂空的智能车底盘，用于相关硬件电路模块的装配（相关模块有电机驱动模块、主控板、传感器采集模块、电容储电模块、万向轮、传感器支架以及电机支架等）。与A车模电轨组类似，为了前后重量均衡，前端有一定伸长量的传感器线圈获取赛道信息，中间是主控板，后端即使电机驱动部分，与两驱动轮相邻。在实现做出相关模块后，为了达到高精度的装配效果，防止发生干涉现象，我们在catia v5R20软件里进行了建模仿真，各模块均用量具测量再输入，最终整体布局如下（传感器线圈模块未显示，应该在固联在两根伸长的碳素杆上面）：

截图1

2.1.1俯视图

截图2

2.1.2侧视图

截图3

2.1.3后视图

2.2智能车底盘设计

为了方便模块的安装（原有安装孔）、减少车重及降低重心的原则，底盘精良精简，能不必要的地方均镂空处理，同时又要有一定外观，所以设计时几乎都是圆滑过渡，这同时也减少了底盘的应力集中二炸裂，增强实用性，地盘初稿如下（cad绘图设计，配合各个模块的安装需要，然后导入catia，生成实体薄板与其他模块装配在一起）：


2.2.1底盘CAD示意图 2.2.2底盘catia示意图

经过装配后，发现效果并不是很好，由于测量误差的影响，电机安装到底盘后，两轴并不重合，成一个小夹角，，并且底盘虽然横向刚度满足要求，但纵向（行车方向）刚度太小，挠度过大，于是有设计一块底盘加固板与电机正下方，一方面加强纵向刚度，一方面加以附属电机的长轴，使之与底盘平面平行，左右两轴轴线重合，改善行驶效率（加强件上除了固定用的安装孔外还有两组小圆孔，用于穿过扎带约束电机长轴而固定在底盘上）如图：

底盘

2.2.3底盘加强件CAD示意图

经强化之后，达到要求。

2.3电机装配

由于所选电机与编码器（减速机构和测速机构）固联为一体，为降低重心，突出的部分尽量朝下，然后电机装在L型金属支架上，防止移动，用螺母将支架固定在底盘上，完成电机的安装，如图所示：


2.3.1 1L型电机支架

2.3.2 电机


2.3.3 电机装配示意图

## 2.4前瞻固定

直接用碳素杆和安装孔固定在底盘两边的空余地方上如图：


2.4.1 碳素杆固定示意图一 2.4.2碳素钢固定示意图二


2.4.3 碳素杆固定示意图三

2.5万向轮安装

固定在底盘下底面直接与赛道接触，如下图（行车方向前端）：


2.5.1 万向轮安装示意图一


2.5.2 万向轮安装示意图二

机械部分如上所述。

# 第三章 硬件电路设计

3.1整流部分

由于赛道上两个导电铝膜所给的电压正负极无法确定，因此，系统采电模块需要进行电源极性矫正，即电刷取电之后需要经过一个二极管全桥。考虑到用肖特基二极管最大有0.55V的压降（SK54），因此搭建的整流桥会产生约1.1V的电压损耗。假设系统正常工作电流4A，则在整流部分将会有4.4W的功率以热能的形式耗散。

为此，我们决定采用理想二极管整流桥。配合4个N沟道MOSFET,搭建整流桥。


3.1.1整流电路图一

每个MOSFET开通后内阻3.3mOhm，所以整流桥内阻约6.6mOhm。在同样4A的工作电流下，耗散功率为,为肖特基二极管整流桥的约2.4%。

当输入电压小于LT4320的工作电压（9V）时，LT4320不工作，所有MOSFET不开通，电路通过MOSFET内部的二极管进行整流。整流桥压降约1V。


3.1.2整流电路图二

3.2大电容储能

考虑到在十字交叉部分或者其他意外短路可能造成暂时的断电，为此，在整流之后加入大电容进行储能。以保证在断电后能够维持系统工作一段时间。同时，在加入大电容后，容性负载上电瞬间将会产生很大的电流，有引起赛道电源断电的可能。因此我们在电路中串入一个电感，和一个自恢复保险管来抑制电流的迅速上升。

3.3 Buck变换

赛道电源提供12V直流电。但主控电路需要的电压主要为5V和3.3V。从12V降压到5V，如果使用传统的线性稳压,假设主控电路消耗电流500mA，那么将会有约的功率以热能形式耗散。这里我们采用buck电路将12V开关稳压到5V。


3.3.1 buck电路示意图

假设buck变换的效率为80%（参考LM2596-5（TI）），则buck变换的开关损耗为，为线性稳压的17.8%

## 3.4电动机软起动，电流环准时间最优控制反馈电路

由题目要求可知，当铝膜中的电流大于5A时，赛道电源将会中断输出。因此我们需要限制系统最大电流。

由于在电动机启动瞬间及发生意外堵转等情况时，能够产生相当可观的瞬时电流。

因此，我们的电动机不能直接启动，而应该软起动的方法。但是该方法必然将严重削弱电动机的启动速度。为此，我们对电动机采用转速、电流双闭环反馈控制的方式，在启动及运行过程中对电动机的电枢电流进行监控。

首先人为设定一个最高电流，在这个电流上进行启动。

启动步骤如下：

电流上升阶段：当给定一个目标速度时，在转速调节器和电流调节器的作用下，电动机输入电压，输入电流迅速上升，当电流达到负载电流后，电动机开始转动，并不断加速，当电流达到电流调节器设定最大电流后，电压下降，电流稳定在允许的最大值，进入恒流升速状态。

恒流升速阶段：由于转矩与电流成正比，在此阶段，电流一直保持最大设定值，相当于输出转矩不变，小车速度线性增长，当达到目标速度后，进入转速调节阶段。

转速调节阶段：当车速到达给定值，电动机电压和电流开始下降。系统逐步进入稳定状态。

利用该方法，可以在设备最大电流允许的条件下实现最短时间的控制，即准时间最优控制。

为了检测电机电流，我们在电动机电枢绕组中各串联一个霍尔电流传感器ACS712-5。使用单片机AD读取反馈电压，计算实时电流大小。

为了反馈电机转速，我们采用了增量式编码器检测电机转速。

3.5取电方案

3.5.1使用碳刷取电

3.5.1.1碳刷

经过测试，所用碳刷内阻1Ω，工作状态合电阻2Ω。假设工作电流3A，通过计算，在电刷上的压降为6V，显然不合理。

3.5.2使用单根导线

假设采用单根导线做电刷的方案电路内总电阻为1Ω，由此将造成电动机机械特性变软，如图中红线所示。


3.5.2.1碳刷机械性能分析图

3.5.3采用集束导线

将多根导线捆扎集束后，作为一个电刷，能够大大减小导线内阻。减小电阻带来的电能损耗后电机特性变软。

经过分析比较，决定采用集束导线做电刷。

3.6主控方案

采用恩智浦Kinetis L系列超低功率微处理器，并在使用时根据需求适当采用降低内核频率，进入低功耗模式，关闭多余的外设时钟，合理进行任务调度，完成实时控制后，进入等待模式等方法降低系统功耗。

# 第四章 控制软件设计说明

4.1程序流程图


4.1.1程序流程图

4.2循迹算法

赛道是由两条铝膜构成，我们通过线圈检测铝膜的位置来判断小车所在的位置。通过读取LDC1614寄存器的值，得到三个线圈与各自电容组成的谐振电路的振荡频率。当线圈下方有金属铝膜时，谐振频率会发生改变，且变化大小和覆盖面积有关。

因此我们通过静态采集小车与赛道偏移位置的大小与三个线圈两两读数之差的关系，获得一系列数据点，并进行三次多项式拟合。得到线圈读数和小车位置的多个关系公式，再用一些特征点最终判断小车的正确位置。


4.2.1检测示意图

4.3速度和转向控制

小车是由两个伺服电机和一个支撑用万向轮组成的。在允许的调速范围内，可以使用增量式PI算法，分别控制两个电机的转速。在实际赛道上，首先设定一个基础速度，在弯道时，使用外环的pid根据当前位置偏差获得一个差速值，将此差速值分别正负叠加到速度内环的给定上，使左右轮产生差速从而实现转弯。

# 第五章 开发工具调试过程说明

5.1电能检测装置

为了测量运行过程中消耗的电能，我们独立设计了一个嵌入式电能检测控制系统。

该系统采用K60处理器，独立电源供电，经过霍尔电流检测芯片ACS712-5实时监测赛道上的电流。通过电磁继电器控制赛道的通电与否。

系统上电时，在断开电源状态下连续采集电流传感器零点，完成后闭合继电器，给赛道上电，对电流进行积分，并使用OLED显示电能消耗情况.赛车出发后，检测是否过流，如发生过流，关闭继电器并报警。

# 第六章 模型车的主要技术参数说明

6.1智能车外形参数

长35cm，宽22cm，高3cm。

6.2电路部分参数

7个电解电容储能约0.03F,正常工作功率6W。

6.3传感器个数以及种类

3个漆包线线圈，2个编码器，3个干簧管。

6.4赛道信息检测精度，频率

检测精度1cm，频率10ms。

6.5电机参数和选型

由于他励直流电机控制方便，根据理论可知：

直流电机转速特性公式

，

直流电机转矩特性公式

两个常数的关系：

由于电机励磁方式为他励，因此，,是由电机本身的结构特性决定的，需要在电机选型时进行测试，转矩和电流成正比，同时电枢回路电阻尽量小，能够获得更加硬的机械特性。

将待测电机和同一个电机同轴连接。待测电机直接接到12V稳压源，工作在正向电动状态，另一个电机的电枢串联功率电位器，工作在发电状态。调节电位器，调整发电机负载从空载到重载，记录电动机电枢电流大小和转速。测试几种电机特性

6.5.1带减速箱的maxon空心杯电机

电机电枢内阻为22.1Ω，额定电压为24V，实际在12V下使用，因此在12V下带减速箱测试其特性曲线，数据如下：


6.5.1.1 Maxon空心杯电机测试数据

特性曲线线性度极佳。

6.5.1.2 Maxon空心杯电机特性曲线

由测试数据可以得到

由此可知该电机在带减速箱外接12V电压的情况下的理想空载转速为287r/min，

6.5.2 RS-380电机性能测试

由于该电机电流较大，实验室设备功率有限，所以采用降电压测试，再用公式推算的方法。在1.19V下测试数据如下：

6.5.2.1 RS-380电机测试数据

6.5.2.2 RS-380电机特性曲线

由测试数据可以得到：

计算可得：

由此可以推算该电机在12V时的特性如下：

参考规则要求，决定选用maxon电机更为合适。

# 第七章 结论与反思

本作品初步设计为采用LT4320和四个场效应管搭建的理想二极管整流桥对赛道电源做极性矫正，消除了二极管压降带来的损耗。采用buck变换将电压从12V稳压到5V，使用线性稳压将5V稳压到3.3V,在减小能耗和抑制电源纹波上取得平衡。处理器采用恩智浦公司的KL25系列低功耗单片机，在算法控制上合理运用了低功耗模式，并合理地设置系统时钟，最大限度地降低了系统功耗。小车运动采用两个空心杯伺服电机差速驱动和一个球式万向轮支撑，在速度和功耗上取得平衡。循迹采用LDC系列电感数字传感器，能够非常精确地识别赛道。

在调试过程中，也出现一些问题需要之后的时间里继续改进：

所选电机减速比过大，限制了所能达到的最高速度。需要之后更换电机型号或者采用更为复杂的buck-boost电路提高调速性能。

集束导线制作的电刷体积大于两条铝膜的缝隙，小车内切入弯可能短路两条铝膜导致断电。需要在之后改用电刷阵列来避免。

在这几个月的准备过程中，我们感到通过创意赛大大提高了自己的工程实践能力和创造能力。学会了根据实际需要，设计合适的电路。并对电力电子有了初步的认识。

在这几个月的备战中，在场地、经费方面都的到了学校的大力支持， 在此特别感谢一直支持和关注智能车比赛的学校领导以及各位老师。同时也感谢比赛组委会能组织这样一项很有意义的比赛。

# 附录

电机驱动


8.1.1电机驱动电路图

取电电路


8.1.2取电电路图

主控电路：


8.1.3主控电路图

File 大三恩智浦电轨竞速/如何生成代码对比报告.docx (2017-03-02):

# 如何生成代码对比报告

——李锐戈

当新工程出现bug时，可以使用liunx的文件比较功能与老工程的代码进行比对，方便定位bug。

软件平台：Linux操作系统

1、 使用树莓派
2、 使用虚拟机安装ubuntu

以Ubuntu为例：

1、 最好有个固态硬盘，安装VMware虚拟机
2、 下载Ubuntu镜像，版本无所谓，在VMware中安装并完成配置。
3、 打开虚拟机


4、 在主目录下新建一个文件夹，并更改其权限。
1） 打开终端（命令行）


cd / 回到根目录

ls 查看根目录文件确认所在的位置正确


2） sudo mkdir mission 根目录需要最高权限 因此需要声明sudo

mkdir建立文件夹

建立mission文件夹


因为要求了最高权限，所以要输入密码，这里输入时不会显示。

ls 查看当前文件夹下目录确认建立了

3） 更改mission文件夹权限

sudo chmod -R 777 /mission

这样，操作这个文件夹就不一定需要在命令行用sudo命令操作了

5、 为了方便使用，安装VMware Tools


cd /media/whutddk/'VMware Tools' 进入加载的工具文件夹，具体位置根据系统设 置有所不同，最后一个位置带单引号是因为带 了空格

ls 查看当前文件夹的内容确认

cp VMwareTools-10.0.5-3228253.tar.gz /mission 将文件复制到mission文件夹

cd /mission 进入/mission

ls 查看内容确认

tar -xzf VMwareTools-10.0.5-3228253.tar.gz 解压文件，具体参数意义自行百度linux的tar 命令


cd vmware-tools-distrib 进入文件夹


sudo ./vmware-install.pl ./表示当前文件夹

按照提示输入yes，no来完成安装，然后重启虚拟机，完成配置

6、 建立对比文件夹

cd /mission 进入mission文件夹

mkdir old 建立old文件夹

mkdir new 建立new文件夹


我之前已经将vmtools安装文件夹删除了

7、 从windows复制需要比对的代码到old和new文件夹

因为有VWtools，所以可以直接在windows里面点复制，在Ubuntu里点粘贴。


8进行比对

cd /mission

diff -r old new diff是比对命令，-r表示比对子目录，还有其他参数可以设置


结果具体到哪个文件的第几行

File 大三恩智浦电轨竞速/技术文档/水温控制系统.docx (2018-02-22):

题号：E

武汉理工大学第八届电工电子

创新设计大赛设计报告

题目：水温控制系统（E题）

参赛者：李锐戈

学院班级：自动化学院自动化zy1301班

联系方式：18707169086

评分标准：

项目 | 满分
设计与总结报告：方案比较，理论分析与计算，电路图及有关设计文件，测试方法与仪器，测试数据及测试结果分析 | 80
附上仿真图或实物效果图 | 20

摘要

根据题目要求，采用K60处理器，利用温度传感器DS18B20，实时测量水的温度，根据模糊控制的策略，通过控制继电器的通断，来调整加热棒的输出功率，达到控制目标温度的目的。

关键字：K60处理器 温度传感器 模糊控制

# 1系统方案

## 1.1系统设计

### 1.1.1系统原理分析

根据题目要求，通过温度传感器实时监测当前温度数据，与给定目标值进行比较，当温度降低，或给予风扇降温等扰动，或给予阶跃的给定目标值时，根据当前与给定的差值和当前温度差值的变化率，利用模糊控制算法，控制加热棒的输出功率。从而使水温能够稳定或者跟随给定目标。

### 1.1.2系统结构框图


## 1.2方案选择

### 1.2.1处理器方案

方案一：采用51单片机，这种单片机成本极低，最小系统电路简单，程序容易编写。但存在运算能力不足，外设不足等缺点。

方案二：采用K60处理器。这种ARM架构的处理器电路和程序比较复杂，成本较高。但运算速度快，外设丰富，在系统设计时有较大的灵活性。

通过比较分析，认为采用方案二较为合适。

### 1.2.2温度传感器方案

方案一：采用TI公司的LM19传感器，该传感器供电电压为+2.4V到+5.5V，量程范围-55℃到+130℃，采用模拟输出，因此需要使用ADC采集，采集温度可以根据输出电压可由技术手册公式计算得到。

方案二：采用TI公司的LM135传感器，该传感器的测量范围为−55℃到150℃，采用模拟输出，需要搭建外围检测电路，并可以使用外围电路校准输出温度。测量误差为0.3℃。

方案三：采用DS18B20，该传感器是数字输出，测量范围-55℃到125℃，可采用寄生电源工作方式而不需要外部电源供电，因此只需要一条数字信号线和一条地线即可完成测量。测量精度为0.0625℃，转换时间较长且由转换精度决定。

通过比较分析，决定采用方案三即DS18B20的方案，该方案硬件电路简单，测量精度高。虽然转换时间较长，但由于本系统时间常数大，传感器转换时间对控制影响不大。

### 1.2.3控制方案

方案一：采用PID控制，比例积分微分控制是一种非常通用的控制算法，对于线性定常系统有比较好的控制效果。它不需要系统的模型，参数一般可以通过现场整定得到。其缺点也比较明显，即对较复杂的系统控制效果比较差。性能指标较难达到。

方案二：采用离线生成模糊控制表，在线查表的控制方式。模糊控制可以模拟人工控制的过程。可以根据专家经验，大大改善系统性能，提高响应速度和超调。通过matlab离线建立模糊控制的规则表和隶属度函数，并导出为控制表。将控制表导入到控制系统中，在控制时，根据输入查表即可得到输出。该方案对处理器的运算速度要求很小，但控制规则表和隶属度函数的整定较为麻烦。

方案三：采用在线计算的模糊控制。相对于离线生成，在线查表的模糊控制方法。该方案则是直接将模糊控制的运算写入软件代码，进行实时运算和控制。通过上位机，可以实时修改模糊规则和隶属度函数，方便调试，但处理器的运算量将会非常大。

根据题目要求，通过对比分析，模糊控制才能获得更好的控制效果，为了方便调试，并且考虑到K60的优秀的运算性能，决定采用方案三。

### 1.2.4加热方案

方案一：采用小功率直流电热棒，通过开关调压电路控制输入电压来控制输出的功率。

方案二：采用大功率交流电热棒，通过交流调功控制输出功率。

考虑到水的比热容为4.2×10³ J/(kg℃)，即每升高1℃需要4200J热量。在不考虑热量散失及效率100%的理想条件下，从40℃升至60℃需要84000J，需要500W的电热棒加热2.8分钟。因此需要使用比较大功率的加热设备才能满足题目的要求，并考虑到系统的时间常数比较大，选择方案二。

# 2软件设计

## 2.1模糊控制算法

### 2.1.1温度偏差（Terror）隶属度函数

初步建立温度偏差隶属度函数如图所示。当前水温和目标水温的差值分为四级，负大（NB），负中（NM），负小（NS），正（P），将输入温度偏差模糊化。


### 2.1.2温度差值变化率（Dif）隶属度函数

初步建立本次采样水温较上次水温的差值隶属度函数如图所示，共分五级：负大（NB）,负小（NS），零（Z），正小（PS）,正大（PB），将温度差值变化率模糊化。


### 2.1.3输出功率（OUT）隶属度函数

初步建立输出给加热器的功率隶属度函数如图所示。共分五级，分别为小（S），半小（HS）中（M），半大（HB），大（B）。其中最小输出为0，最大为12。


### 2.1.4模糊控制规则的建立

水温控制系统的时间常数较大，因此在水温与设定值相差比较大时（Terror = NB），加热器应该饱和输出（OUT = B），以提高响应速度。当水温高于设置时（Terror = P），加热器应该使用小输出甚至停止输出（OUT = S）以抑制超调。

当水温低于设定值但差距不大时，应该根据偏差和偏差变化率控制加热器的输出，提高系统的指标。

由此初步建立模糊控制规则表如图所示。


### 2.1.5模糊结果的计算

当模糊推理结束后需要进行反模糊处理，输出需要的结果，这里采用比较常见的重心法解模糊。通过计算重心点所在位置来得出模糊结果。

## 2.2软件流程图


# 3硬件设计

## 3.1 处理器

使用自制的K60最小系统核心板，其自带稳压芯片，有防止过流过压及反接电路。自带蓝牙接口，LED指示灯等，方便调试。原理图见附录。

## 3.2加热电路

用带光耦隔离的继电器控制加热棒，给继电器输入低频的PWM信号，利用开关原理进行交流调功，控制加热棒的输出功率。

## 3.3温度传感器

使用一个带防水套的DS18B20数字温度传感器，将其VCC和GND同时接地，信号线接IO口。使其工作在寄生电源模式。利用IO口模拟通信时序，读出传感器所测得的值。

## 3.4显示模块

题目要求实时打印温度曲线，因此加入液晶显示模块，使用12806液晶，与处理器进行SPI通信，控制简单可靠。

# 4系统仿真测试

在simulink中建立模糊控制仿真模型如下


取一些典型的输入，在systemtest中测试其输出。观察输出是否合理。


从测试结果可以看出，输出是符合预期的。

# 5参数调试

利用之前为模糊控制调试而设计的上位机。可在线实时微调隶属度函数和模糊规则表。根据经验调试，使系统达到稳态误差小，动态响应快，超调小的题目要求。


# 6结果分析

由于系统采用了模糊控制的算法，因此系统性能极佳，具有良好的动态特性和静态特性。温度控制的静态误差小于0.2℃。当设定温度突变时，系统调节时间和超调量很小。加上12864液晶的配合，可以实时显示温度和自动打印水温随时间变化的曲线。


# 参考文献

[1]胡寿松主编 自动控制原理（第四版）科学出版社，2001

[2]王兆安 刘进军主编 电力电子技术（第五版）机械工业出版社 2015

[3]张晓华主编 控制系统数字仿真与CAD（第3版）机械工业出版社 2016

# 附录

主控板原理图：


模糊控制代码节选：

#define T_NB 0 #define T_NM 1 #define T_NS 2 #define T_P 3

#define D_NB 0 #define D_NS 1 #define D_Z 2 #define D_PS 3

#define D_PB 4 #define O_NB 0 #define O_HB 1 #define O_M 2

#define O_HS 3 #define O_S 4

uint8 rule_list[4][5] =

{ //D_NB D_NS D_Z D_PS D_PB

{O_B, O_B, O_B, O_B, O_B}, /* T_NB */

{O_B, O_B, O_HB, O_M, O_HS }, /* T_NM */

{O_HB, O_M, O_HS, O_S, O_S}, /* T_NS */

{O_S, O_S, O_S, O_S, O_S} /* T_P */

};

float T_memf[4][3] =

{

{-10, -1.5, -0.1}, //T_NB

{-1.5, -0.9, -0.3}, //T_NM

{-0.1, -0.3, 0}, //T_NS

{-0.2, 0, 10} //T_P

};

float D_memf[5][3]=

{

{-10, -0.1, -0.05}, //D_NB

{-0.1, -0.05, 0}, //D_NS

{-0.05, 0, 0.05}, //D_Z

{0, 0.05, 0.1}, //D_PS

{0.05, 0.1, 10}, //D_PB

};

float O_memf[5][3] =

{

{-3., 0., 3.}, //O_B

{0, 3., 6.}, //O_HB

{3., 6., 9.}, //O_M

{6., 9., 12.}, //O_HS

{9., 12., 15.} //O_S

};

//对当前输入求所有输入隶属度三角形的面积并遍历规则表进行模糊推理得出输出隶属度三角

for ( i = 0 ;i < 4; i++ ) //Terror

{

for ( j = 0;j < 5; j++ ) //Dif

{

if ( E_DATA > T_memf[i][0] && E_DATA < T_memf[i][2]

&& EC_DATA > D_memf[j][0] && EC_DATA < D_memf[j][2] )

{

if ( E_DATA <= T_memf[i][1] )

{

e_temp = (1./(T_memf[i][1]-T_memf[i][0])) * (E_DATA - T_memf[i][0]);

}

else

{

e_temp = (1./(T_memf[i][1]-T_memf[i][2])) * (E_DATA - T_memf[i][1])+1;

}

if ( EC_DATA < D_memf[j][1] )

{

ec_temp = 1.0/(D_memf[j][1]-D_memf[j][0]) * (EC_DATA - D_memf[j][0]);

}

else

{

ec_temp = (1./(D_memf[j][1]-D_memf[j][2]))* (EC_DATA - D_memf[j][1])+1;

}

//遍历规则表

result[rule_list[i][j]] += e_temp * ec_temp;

}

}

}

//反模糊，重心法

u_temp += result[0]*1* ( ( (O_memf[0+1][0] -O_memf[0][2] )/ 2 + O_memf[0][2] ) - O_memf[0][0]) * O_memf[0][1];

u2_temp += result[0]* ( ( (O_memf[0+1][0] - O_memf[0][2] )/ 2 + O_memf[0][2] ) - O_memf[0][0]);

for(i=1;i<4;i++)

{

u_temp += result[i]*1*( ( (O_memf[i+1][0] -O_memf[i][2] )/ 2 + O_memf[i][2] )

- (( O_memf[i][0] - O_memf[i-1][2])/2+ O_memf[i-1][2]) ) * O_memf[i][1];

u2_temp += result[i]*1*( ( (O_memf[i+1][0] -O_memf[i][2] )/ 2 + O_memf[i][2] )

- (( O_memf[i][0] - O_memf[i-1][2])/2+ O_memf[i-1][2]) );

}

u_temp += result[4]*1* ( O_memf[4][2] - ((O_memf[4][0] - O_memf[3][2])/2 + O_memf[3][2]) ) * O_memf[4][1];

u2_temp += result[4]*1* ( O_memf[4][2] - ((O_memf[4][0] - O_memf[3][2])/2 + O_memf[3][2]) );

output = (u_temp / u2_temp);

return (output);

}

系统部分照片：



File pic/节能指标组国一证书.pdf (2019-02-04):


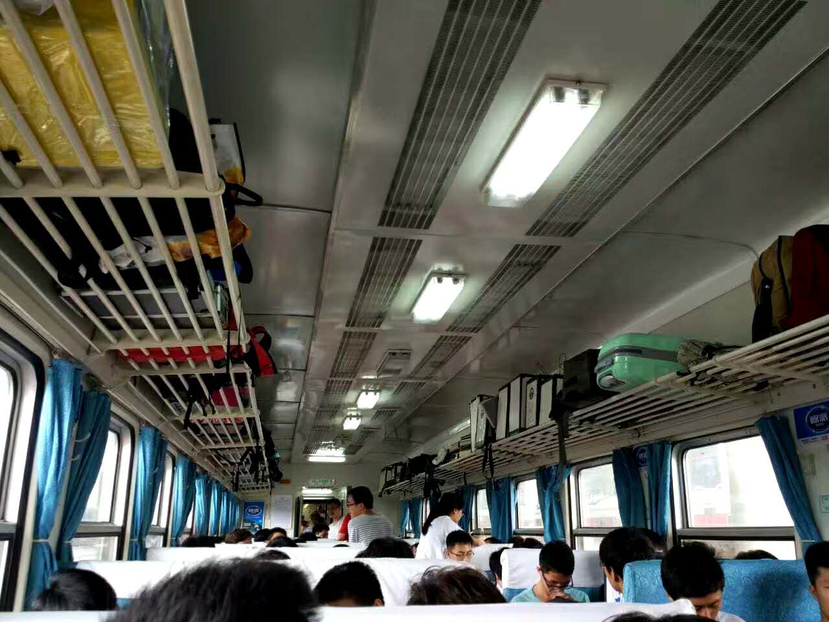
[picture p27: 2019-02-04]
pic/微信图片_201901312200224.jpg

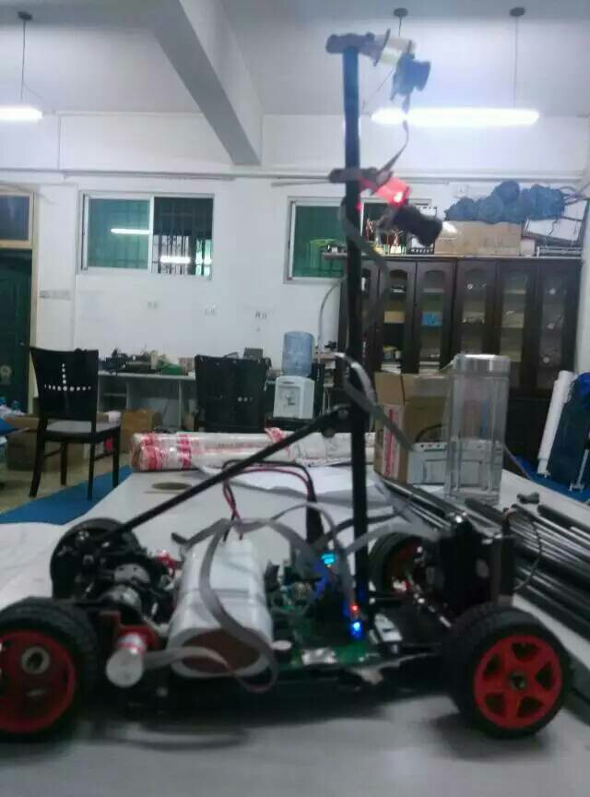
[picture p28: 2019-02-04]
pic/mmexport1465473615614.jpg

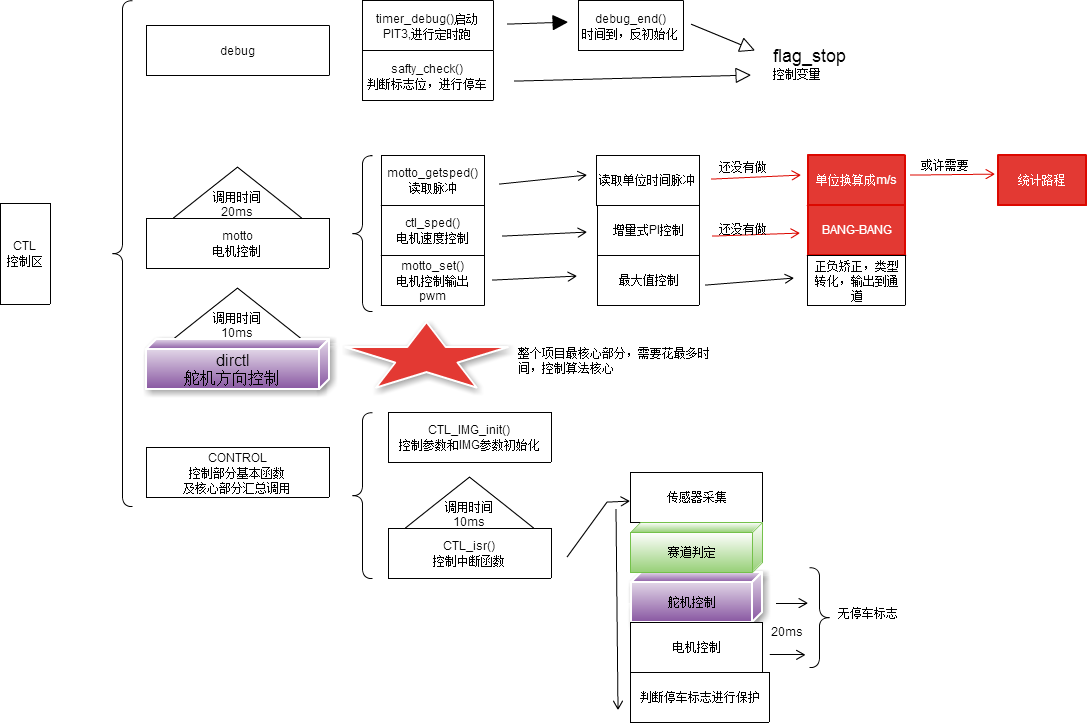
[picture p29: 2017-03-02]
大三恩智浦电轨竞速/软件代码/freescale_cup(DMA)1.0/CTL一览.png

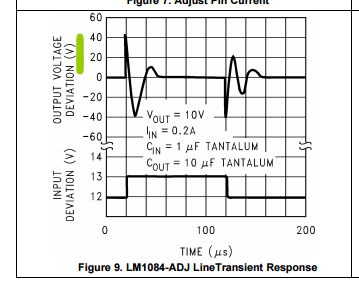
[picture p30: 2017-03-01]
大三恩智浦电轨节能指标晨风/技术文档/QQ截图20160730173043.png

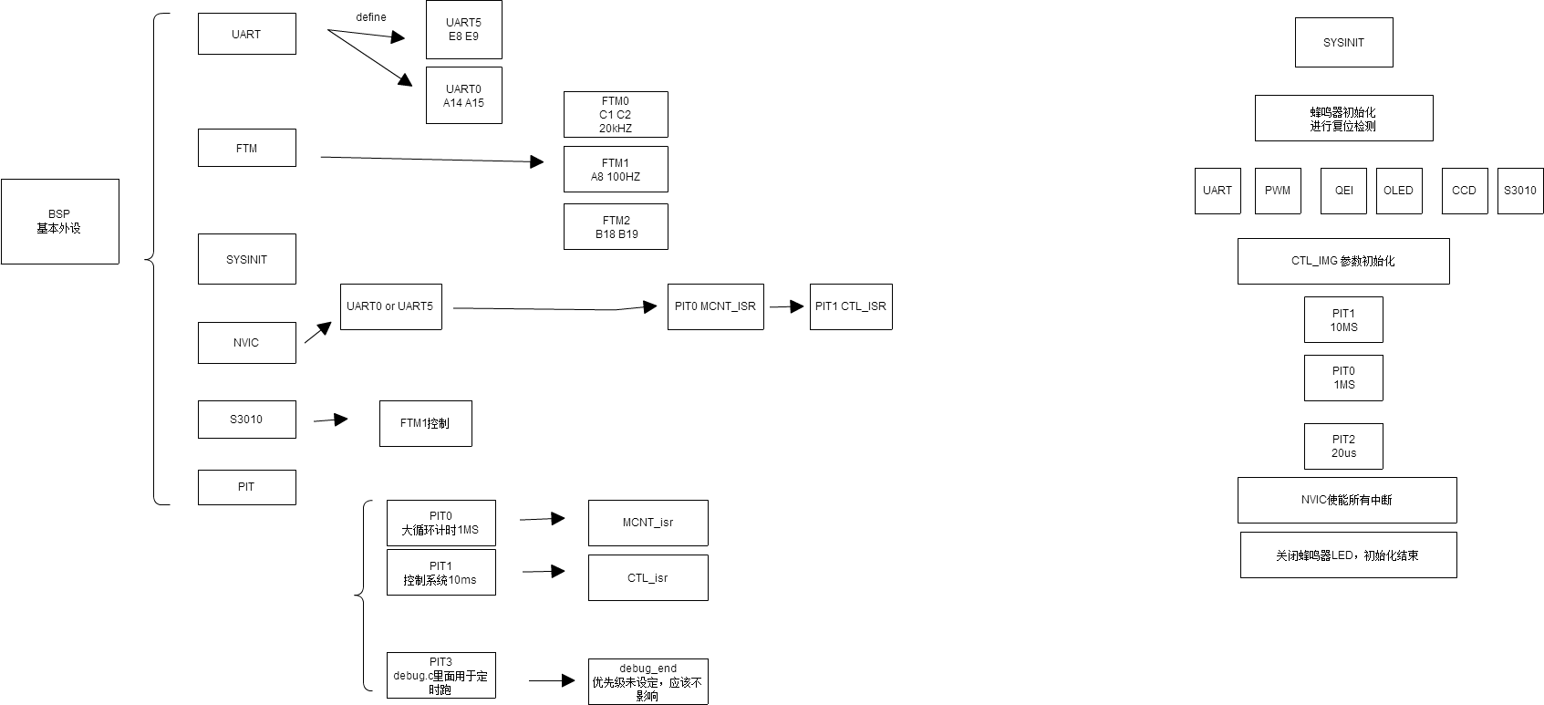
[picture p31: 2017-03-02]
大三恩智浦电轨竞速/软件代码/freescale_cup(DMA)1.0/BSP.png

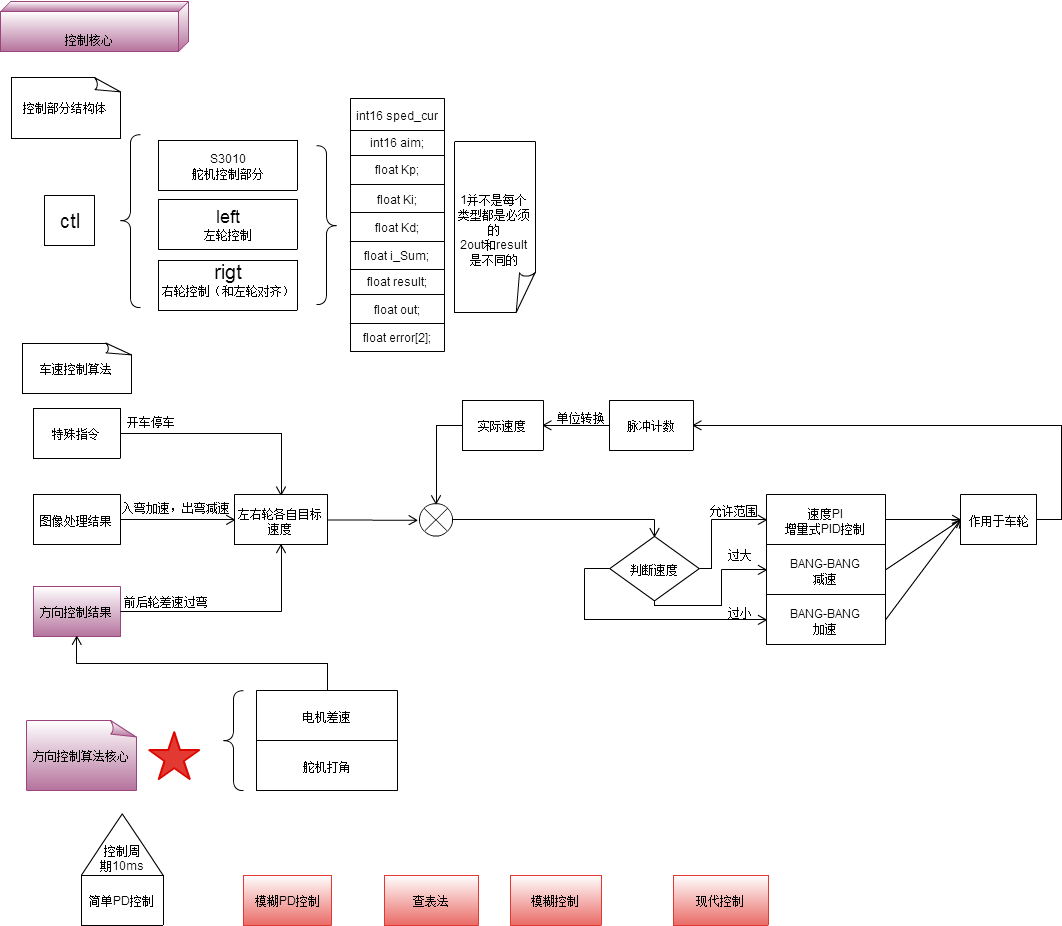
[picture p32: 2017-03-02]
大三恩智浦电轨竞速/软件代码/freescale_cup(DMA)1.0/控制部分核心.png

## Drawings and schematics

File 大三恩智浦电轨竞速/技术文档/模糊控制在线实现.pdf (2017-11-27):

# 模糊控制在线实现

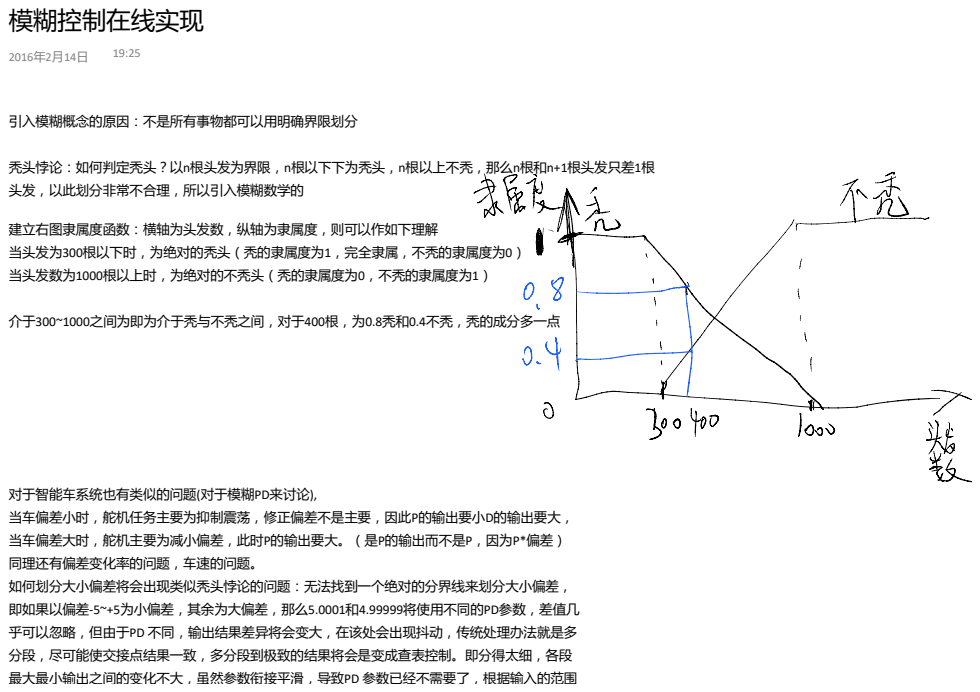
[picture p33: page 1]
引入模糊概念的原因：不是所有事物都可以用明确界限划分; 介于300~1000之间为即为介于秃与不秃之间，对于400根，为0.8秃和0.4不秃，秃的成分多一点

秃头悖论：如何判定秃头？以n根头发为界限，n根以下下为秃头，n根以上不秃，那么n根和n+1根头发只差1根
头发，以此划分非常不合理，所以引入模糊数学的

建立右图隶属度函数：横轴为头发数，纵轴为隶属度，则可以作如下理解
当头发为300根以下时，为绝对的秃头（秃的隶属度为1，完全隶属，不秃的隶属度为0）
当头发数为1000根以上时，为绝对的不秃头（秃的隶属度为0，不秃的隶属度为1）

对于智能车系统也有类似的问题(对于模糊PD来讨论),
当车偏差小时，舵机任务主要为抑制震荡，修正偏差不是主要，因此P的输出要小D的输出要大，
当车偏差大时，舵机主要为减小偏差，此时P的输出要大。（是P的输出而不是P，因为P*偏差）
同理还有偏差变化率的问题，车速的问题。
如何划分大小偏差将会出现类似秃头悖论的问题：无法找到一个绝对的分界线来划分大小偏差，
即如果以偏差-5~+5为小偏差，其余为大偏差，那么5.0001和4.99999将使用不同的PD参数，差值几
乎可以忽略，但由于PD 不同，输出结果差异将会变大，在该处会出现抖动，传统处理办法就是多
分段，尽可能使交接点结果一致，多分段到极致的结果将会是变成查表控制。即分得太细，各段
最大最小输出之间的变化不大，虽然参数衔接平滑，导致PD 参数已经不需要了，根据输入的范围

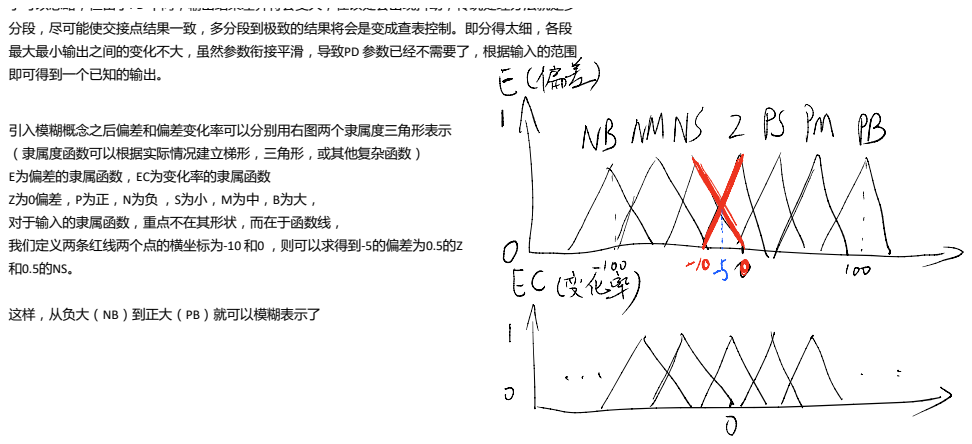
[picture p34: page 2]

乎可以忽略，但由于PD 不同，输出结果差异将会变大，在该处会出现抖动，传统处理办法就是多
分段，尽可能使交接点结果一致，多分段到极致的结果将会是变成查表控制。即分得太细，各段
最大最小输出之间的变化不大，虽然参数衔接平滑，导致PD 参数已经不需要了，根据输入的范围
即可得到一个已知的输出。

引入模糊概念之后偏差和偏差变化率可以分别用右图两个隶属度三角形表示
（隶属度函数可以根据实际情况建立梯形，三角形，或其他复杂函数）
E为偏差的隶属函数，EC为变化率的隶属函数
Z为0偏差，P为正，N为负 ，S为小，M为中，B为大，
对于输入的隶属函数，重点不在其形状，而在于函数线，
我们定义两条红线两个点的横坐标为-10 和0 ，则可以求得到-5的偏差为0.5的Z
和0.5的NS。

这样，从负大（NB）到正大（PB）就可以模糊表示了

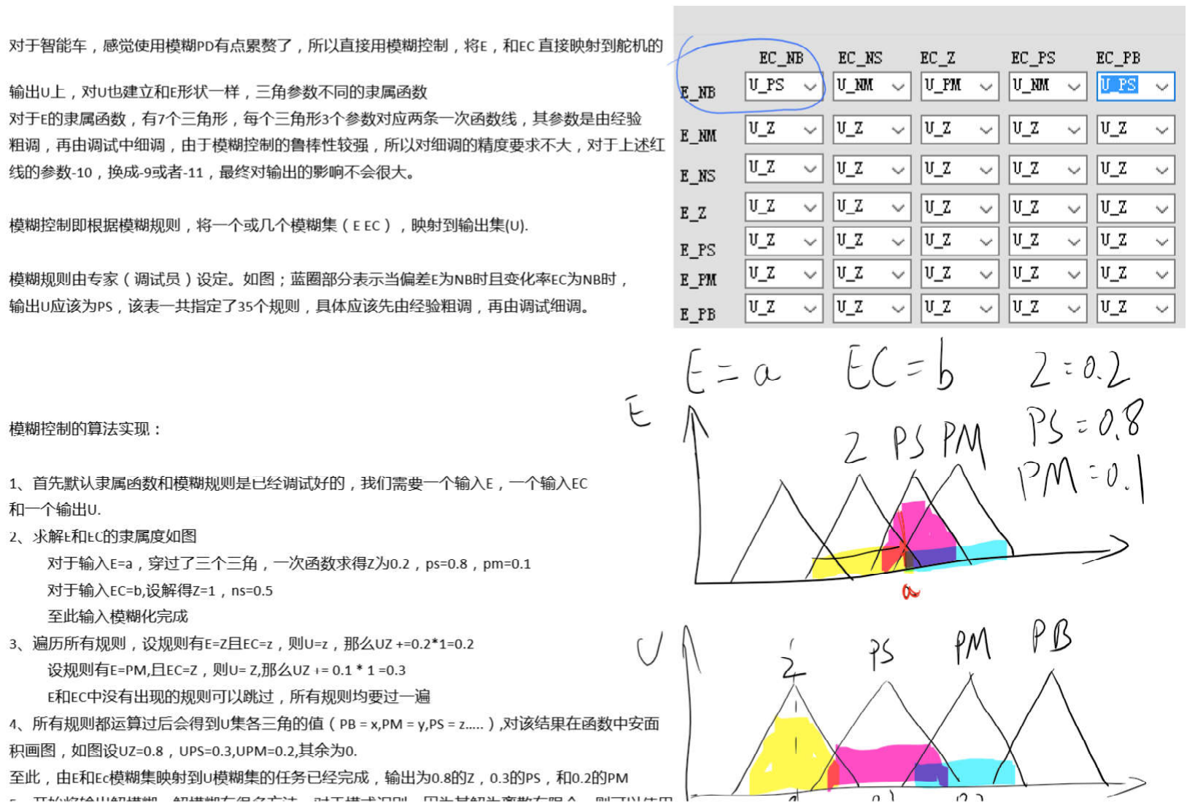
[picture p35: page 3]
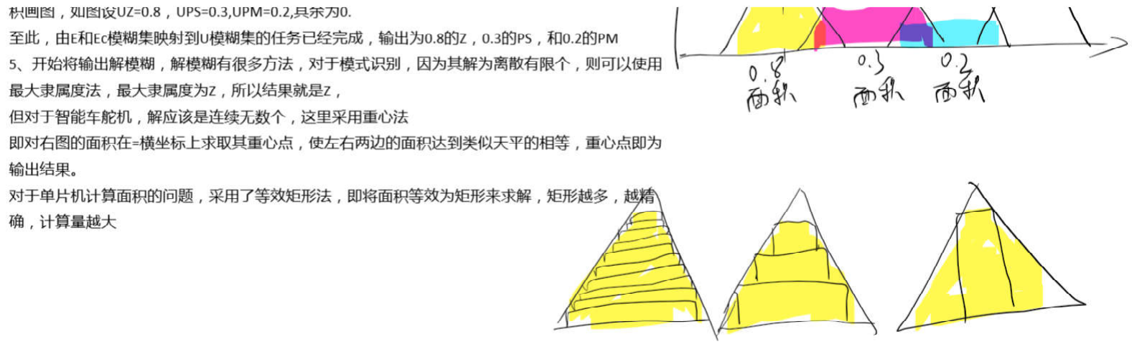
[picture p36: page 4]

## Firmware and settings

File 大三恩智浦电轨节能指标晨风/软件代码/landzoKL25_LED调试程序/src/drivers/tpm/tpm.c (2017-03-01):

/******************** (C) COPYRIGHT 2011 蓝宙电子工作室 ********************
* 文件名       ： adc.c
* 描述         ：工程模版实验
*
* 实验平台     ：landzo电子开发版
* 库版本       ：
* 嵌入系统     ：
*
* 作者         ：landzo 蓝电子
* 淘宝店       ：http://landzo.taobao.com/

**********************************************************************************/
#include "tpm.h"

/*
 * 定义数组
 */

TPM_MemMapPtr TPMN[3] = {TPM0_BASE_PTR, TPM1_BASE_PTR, TPM2_BASE_PTR}; //定义三个指针数组保存 TPMn_e 的地址

//=========================================================================
//函数名称：tpm_enable_int                                                        
//功能概要：使能tpm模块中断。                                                
//参数说明：tpmModule:模块号：0、1、2                                                                                
//函数返回：无
//=========================================================================
void tpm_enable_int(uint8_t tpmModule)
{
	enable_irq(tpm0_irq_no + tpmModule);
}
//=========================================================================
//函数名称：tpm_disable_int                                                        
//功能概要：禁止tpm模块初始化。                                                
//参数说明：tpmModule:模块号：0、1、2                                                                             
//函数返回：无
//=========================================================================
void tpm_disable_int(uint8_t tpmModule)
{
	disable_irq(tpm0_irq_no + tpmModule);
}
//=========================================================================
//函数名称：tpm_init                                                        
//功能概要：初始化tpm模块。                                                
//参数说明：                                                                             
//函数返回：函数执行状态：0=正常；非0=异常
//=========================================================================
void tpm_port_mux(TPMn_e tpmn, TPM_CHn_e ch)
{
    switch(tpmn)
    {
    case TPM0:
        SIM_SCGC6 |= SIM_SCGC6_TPM0_MASK;       //使能TPM0时钟
        switch(ch)
        {
        case TPM_CH0:
            if((TPM0_CH0_PIN == PTC1) || (TPM0_CH0_PIN == PTD0) )
            {
                port_init(TPM0_CH0_PIN, ALT4);
            }
            else if((TPM0_CH0_PIN == PTE24) || (TPM0_CH0_PIN == PTA3) )
            {
                port_init(TPM0_CH0_PIN, ALT3);
            }
            else
            {
                ASSERT(0);                      //设置管脚有误？
            }
            break;

        case TPM_CH1:
            if((TPM0_CH1_PIN == PTC2) || (TPM0_CH1_PIN == PTD1))
            {
                port_init(TPM0_CH1_PIN, ALT4);
            }
            else if((TPM0_CH1_PIN == PTA4) || (TPM0_CH1_PIN == PTE25) )
            {
                port_init(TPM0_CH1_PIN, ALT3);
            }
            else
            {
                ASSERT(0);                      //设置管脚有误？
            }
            break;

        case TPM_CH2:
            if((TPM0_CH2_PIN == PTC3) || (TPM0_CH2_PIN == PTD2) )
            {
                port_init(TPM0_CH2_PIN, ALT4);
            }
            else if((TPM0_CH2_PIN == PTA5) || (TPM0_CH2_PIN == PTE29) )
            {
                port_init(TPM0_CH2_PIN, ALT3);
            }
            else
            {
                ASSERT(0);                      //设置管脚有误？
            }
            break;

        case TPM_CH3:
            if((TPM0_CH3_PIN == PTC4) || (TPM0_CH3_PIN == PTD3) )
            {
                port_init(TPM0_CH3_PIN, ALT4);
            }
            else if((TPM0_CH3_PIN == PTA6) || (TPM0_CH3_PIN == PTE30))
            {
                port_init(TPM0_CH3_PIN, ALT3);
            }
            else
            {
                ASSERT(0);                      //设置管脚有误？
            }
            break;

        case TPM_CH4:
            if(TPM0_CH4_PIN == PTD4)
            {
                port_init(TPM0_CH4_PIN, ALT4);
            }
            else if((TPM0_CH4_PIN == PTC8) || (TPM0_CH4_PIN == PTA7) || (TPM0_CH4_PIN == PTE31) )
            {
                port_init(TPM0_CH4_PIN, ALT3);
            }
            else
            {
                ASSERT(0);                      //设置管脚有误？
            }
            break;

        case TPM_CH5:
            if(TPM0_CH5_PIN == PTD5)
            {
                port_init(TPM0_CH5_PIN, ALT4);
            }
            else if((TPM0_CH5_PIN == PTA0)  || (TPM0_CH5_PIN == PTC9)  ||   (TPM0_CH5_PIN == PTE26)    )
            {
                port_init(TPM0_CH5_PIN, ALT3);
            }
            else
            {
                ASSERT(0);                      //设置管脚有误？
            }
            break;

        default:
            return;
        }
        break;

    case TPM1:
        SIM_SCGC6 |= SIM_SCGC6_TPM1_MASK;       //使能TPM1时钟
        switch(ch)
        {
        case TPM_CH0:
            if((TPM1_CH0_PIN == PTE20) || (TPM1_CH0_PIN == PTA12) || (TPM1_CH0_PIN == PTB0) )
            {
                port_init(TPM1_CH0_PIN, ALT3);
            }
            else
            {
                ASSERT(0);                      //设置管脚有误？
            }
            break;


        case TPM_CH1:
            if((TPM1_CH1_PIN == PTE21) || (TPM1_CH1_PIN == PTA13) || (TPM1_CH1_PIN == PTB1) )
            {
                port_init(TPM1_CH1_PIN, ALT3);
            }
            else
            {
                ASSERT(0);                      //设置管脚有误？
            }
            break;

        default:
            return;
        }
        break;

    case TPM2:
        SIM_SCGC6 |= SIM_SCGC6_TPM2_MASK;                           //使能TPM2时钟
        switch(ch)
        {
        case TPM_CH0:
            if((TPM2_CH0_PIN == PTA1) || (TPM2_CH0_PIN == PTB2) || (TPM2_CH0_PIN == PTB18) || (TPM2_CH0_PIN == PTE22) )
            {
                port_init(TPM2_CH0_PIN, ALT3);
            }
            else
            {
                ASSERT(0);                      //设置管脚有误？
            }
            break;

        case TPM_CH1:
            if((TPM2_CH1_PIN == PTA2) || (TPM2_CH1_PIN == PTB3)|| (TPM2_CH1_PIN == PTB19)|| (TPM2_CH1_PIN == PTE23))
            {
                port_init(TPM2_CH1_PIN, ALT3);
            }
            else
            {
                ASSERT(0);                      //设置管脚有误？
            }
            break;

        default:
            return;
        }
        break;
    default:
        break;
    }
}
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

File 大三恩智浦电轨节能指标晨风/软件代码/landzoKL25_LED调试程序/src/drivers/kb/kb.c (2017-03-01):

//============================================================================
// 文件名称：kb.c                                                          
// 功能概要：键盘构件源文件
// 版权所有: 苏州大学飞思卡尔嵌入式中心(sumcu.suda.edu.cn)
// 版本更新:     时间                     版本                                       修改
//           2012-12-01     V1.0       编写了KL25的键盘驱动
//============================================================================
#include "kb.h"
#include "uart.h"
#include "gpio.h"

//将不连续的引脚用数组表示，使其间接地连贯
//数据口分别接PTC的{11,10,9,8,7,6,5,4}脚
uint_8 KBPin[8]= {11,10,9,8,7,6,5,4};
//键盘4x4按键按键硬件行线列线连接表
const uint_8 KB_CT[4][4]=
{
	{0xEE,0xDE,0xBE,0x7E},
	{0xED,0xDD,0xBD,0x7D},
    {0xEB,0xDB,0xBB,0x7B},
	{0xE7,0xD7,0xB7,0x77},
};
//键盘定义表
const uint_8 KBtable[] =
{
    0xEE,'7',0xDE,'4',0xBE,'1',0x7E,'0',
    0xED,'8',0xDD,'5',0xBD,'2',0x7D,'A',
    0xEB,'9',0xDB,'6',0xBB,'3',0x7B,'B',
    0xE7,'C',0xD7,'D',0xB7,'E',0x77,'F',
    0x00
};
//本版硬件连接全为POTRC
GPIO_MemMapPtr p = PTC_BASE_PTR;

//============================================================================
//函数名称：KBInit
//函数返回：无
//参数说明：无
//功能概要：初始化键盘模块。
//============================================================================
void KBInit(void)
{
    uint_8 i; 
    //本版硬件连接全为POTRC
    //行线低电平（PORTC8~10）
    for(i = 0;i < 4;i++)
    {
    	gpio_init (KBPort, KBPin[i], 0, 0);
    }
    //列线高电平（PORTC4~7）
    for(i = 4;i < 8;i++)
    {
    	gpio_init (KBPort, KBPin[i], 1, 0);
    }
}

//============================================================================
//函数名称：KBScanN
//函数返回：多次扫描键盘得到的键值
//参数说明：重复扫描键盘的的次数(KB_count)
//功能概要：多次扫描键盘，消除"抖动"。
//============================================================================
uint_8 KBScanN(uint_8 KB_count)
{
    uint_8 i,KB_value_last,KB_value_now;
    // 先扫描一次得到的键值,便于下面比较 
    if (0 == KB_count || 1 == KB_count)
        return KBScan1();   
    KB_value_now = KB_value_last = KBScan1();   
    //以下多次扫描消除误差 
    for (i=0; i<KB_count-1; i++)
    {               
        KB_value_now = KBScan1();
        if (KB_value_now == KB_value_last)
            return KB_value_now;                       //返回扫描的键值
        else
            KB_value_last = KB_value_now;
            
    }
    // 返回出错标志 
    return 0xFF;
}
//============================================================================
//函数名称：KBDef
//函数返回：无
//参数说明：键值value 
//功能概要：键值转为定义值函数。
//============================================================================
uint_8 KBDef(uint_8 value)
{
    uint_8 KeyPress;                    //键定义值
    uint_8 i;
    i = 0;
    KeyPress = 0xff;
    while (KBtable[i] != 0x00)          //在键盘定义表中搜索欲转换的键值,直至表尾
    {
        if(KBtable[i] == value)         //在表中找到相应的键值
        {
            KeyPress = KBtable[i+1];    //取出对应的键定义值
            break;
        }
        i += 2;                         //指向下一个键值,继续判断
    }
    return KeyPress;
}

//============================================================================
//函数名称：KBScan1
//函数返回：扫描到的键值
//参数说明：键值valve 
//功能概要：扫描1次4*4键盘,返回扫描到的键值,若无按键,返回0xff 。
//============================================================================
uint_8 KBScan1(void)
{
    uint_8 i,j,tmp;
    uint_32 k = 0,m;
    //键盘初始化
	KBInit();                              
	//最多将扫描4根行线	
	for (i = 0; i <= 3; i++)                           
	{
		if((GPIO_PDIR_REG(p) & (1<<KBPin[i])) == 0)
		{
			//4~7对应引脚列线
			for(j = 4;j <8;j++)
			{
				gpio_set(KBPort,KBPin[j],1);
				//延迟再判断，出去干扰
				for(k = 0;k <5000 ;k++)
					{
						asm("NOP");
					}
					if((GPIO_PDIR_REG(p) & (1<<KBPin[i])) != 0)
					{
						//通过硬件连接表锁定输出值
						if(i < 4 && j < 8)
						{
							tmp = KB_CT[i][j-4];
						}
						else
						{
							tmp = 0;
						}
					}       		
					gpio_set(KBPort,KBPin[j],0);
				}
			}
		}
		for(m=0;m<=21000;m++);
		return (tmp);    
}

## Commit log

2017-05-09 增加一个模糊控制制导文档
2017-11-27 模糊控制在线实现，大三水平，写给学弟看的
2018-02-22 增加水温系统报告
2018-12-27 20181227 资料清查
2019-01-08 Update README.md
    加入蓝宙的视频
2019-01-25 Update and rename 说明.txt to README.md
2019-01-30 清理多余文件
2019-01-30 修改文档
2019-02-04 提供照片

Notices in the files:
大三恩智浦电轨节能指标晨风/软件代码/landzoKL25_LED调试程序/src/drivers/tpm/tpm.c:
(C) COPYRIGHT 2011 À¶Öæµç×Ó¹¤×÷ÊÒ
